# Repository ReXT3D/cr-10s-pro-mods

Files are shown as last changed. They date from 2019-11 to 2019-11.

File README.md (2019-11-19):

# Creality CR-10S Pro hardware mods
### Boards
* [Ribbon cable breakdown board](RibbonCable_MB_BreakdownBoard/) - is fully compatible with original transfer board, helps with wiring with non-original motherboards.

changes from fork
- Beefed up trace width where possible. 
- Heater PCB trace has trace on both Front and Back.
- Heater connector changed to  a more standard 5.08mm screw terminal
- and added I2C AT24C256 EEPROM 

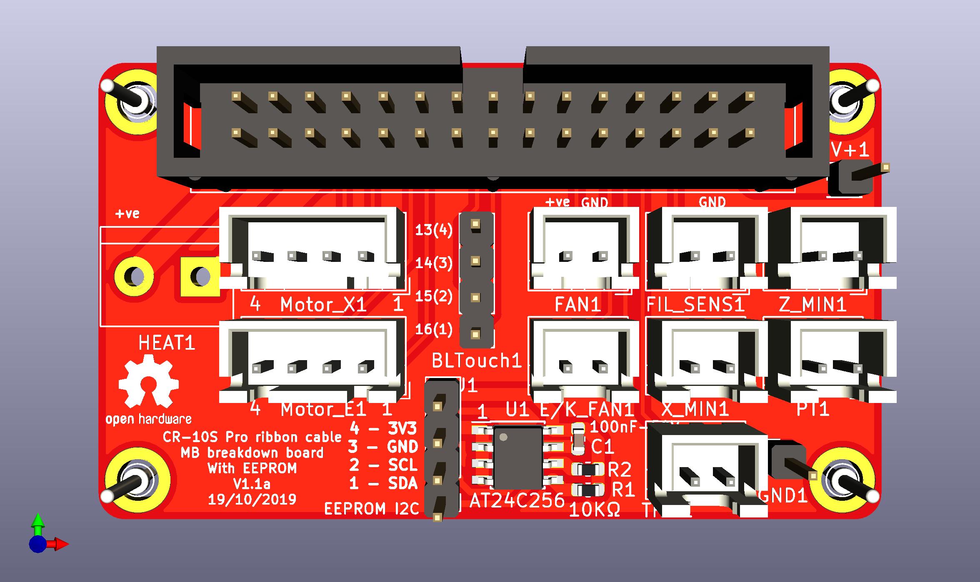
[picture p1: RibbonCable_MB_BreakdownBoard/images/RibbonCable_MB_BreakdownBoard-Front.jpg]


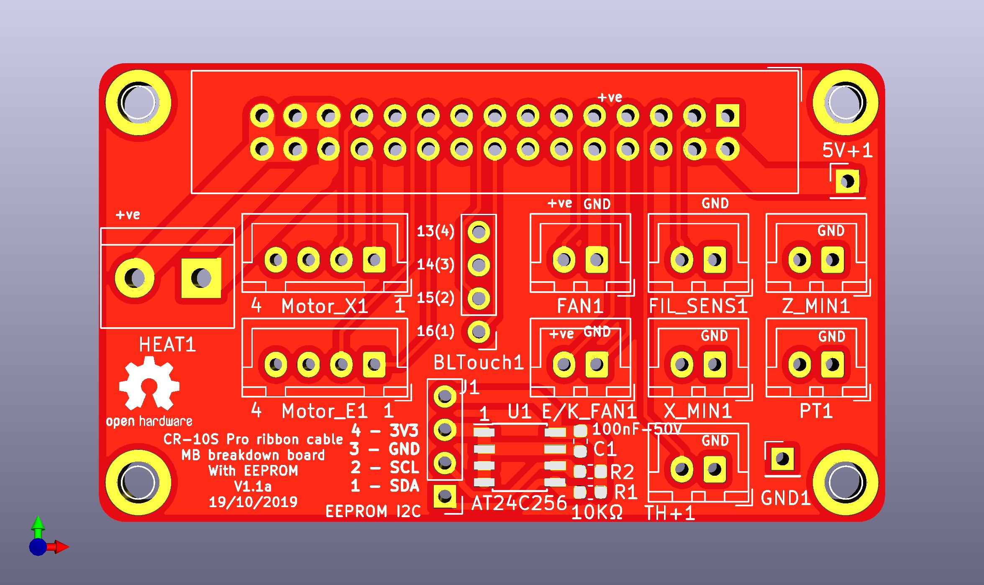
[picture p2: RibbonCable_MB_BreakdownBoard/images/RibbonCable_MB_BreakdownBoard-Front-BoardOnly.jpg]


* [Ribbon cable breakdown board (pt)](RibbonCable_MB_BreakdownBoard_pt/) - "pig tail" soldering oriented, semi compatible with original transfer board, but fully compatible with [Transfer board](Transfer_Board/). Has dedicated 4-wire connection for BLTouch and 3-wire connector for LED.


* [Transfer board](Transfer_Board/) - clean transfer board, compatible with [Ribbon cable breakdown board (pt)](RibbonCable_MB_BreakdownBoard_pt/).


#### Wiring examples
*Coming soon*

#### Ready made boards
*Photos coming soon*

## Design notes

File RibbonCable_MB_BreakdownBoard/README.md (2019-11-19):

# Ribbon cable breakdown board
It is fully compatible with [original transfer board](https://www.aliexpress.com/item/33040303019.html), helps with wiring with non-original motherboards.

FYI, it you just want the gerber files go to 
https://github.com/SkullKill/cr-10s-pro-mods/releases

changes from fork
- Beefed up trace width where possible. 
- Heater PCB trace has trace on both Front and Back.
- Heater connector changed to  a more standard 5.08mm screw terminal
- and added I2C AT24C256 EEPROM 

Front
Front-BoardOnly
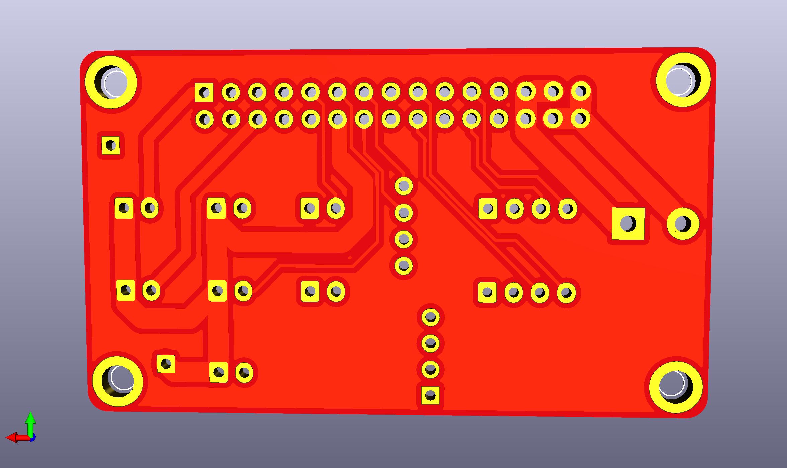
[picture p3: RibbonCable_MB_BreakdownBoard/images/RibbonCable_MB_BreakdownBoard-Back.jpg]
Back

Size

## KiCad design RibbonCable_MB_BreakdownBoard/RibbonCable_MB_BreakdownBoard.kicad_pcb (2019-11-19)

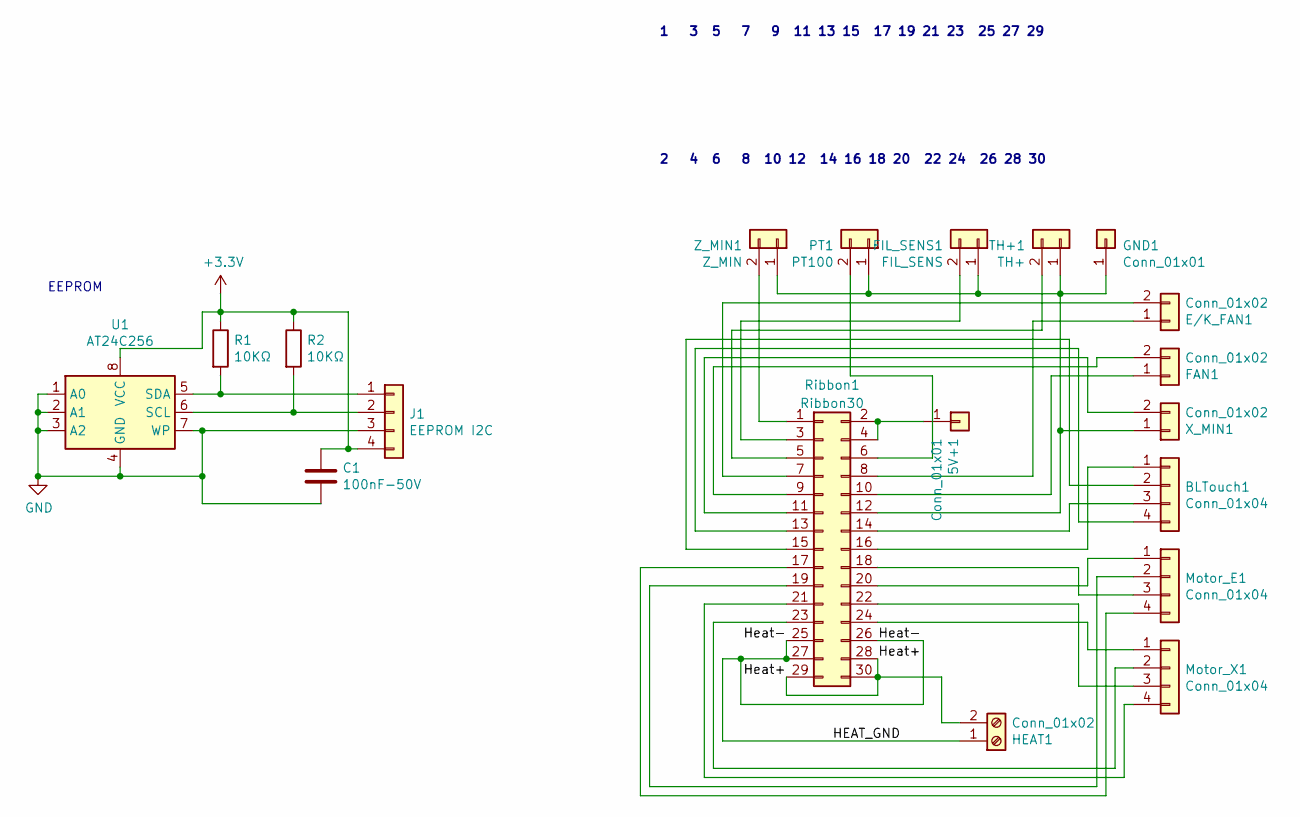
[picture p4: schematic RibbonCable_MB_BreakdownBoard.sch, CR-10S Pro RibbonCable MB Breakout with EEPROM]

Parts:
5V+1: Conn_01x01; PinHeader_1x01_P2.54mm_Vertical
BLTouch1: Conn_01x04; PinHeader_1x04_P2.54mm_Vertical
C1: 100nF-50V; C_0603_1608Metric; MPN AC0603KRX7R9BB104; LCSC C149620
E/K_FAN1: Conn_01x02; JST_XH_B2B-XH-A_1x02_P2.50mm_Vertical
FAN1: Conn_01x02; JST_XH_B2B-XH-A_1x02_P2.50mm_Vertical
FIL_SENS1: FIL_SENS; JST_XH_B2B-XH-A_1x02_P2.50mm_Vertical
GND1: Conn_01x01; PinHeader_1x01_P2.54mm_Vertical
HEAT1: Conn_01x02; TerminalBlock_bornier-2_P5.08mm; MPN KF128-2.54-4P
J1: EEPROM I2C; PinHeader_1x04_P2.54mm_Vertical
Motor_E1: Conn_01x04; JST_XH_B4B-XH-A_1x04_P2.50mm_Vertical
Motor_X1: Conn_01x04; JST_XH_B4B-XH-A_1x04_P2.50mm_Vertical
PT1: PT100; JST_XH_B2B-XH-A_1x02_P2.50mm_Vertical
R1, R2: 10KΩ; R_0603_1608Metric; MPN RC0603FR-0710KL; LCSC C98220
Ribbon1: Ribbon30; IDC-Header_2x15_P2.54mm_Vertical; MPN C79824; LCSC C79824
TH+1: TH+; JST_XH_B2B-XH-A_1x02_P2.50mm_Vertical
U1: AT24C256; SOIC-8_3.9x4.9mm_P1.27mm; MPN AT24C256C-SSHL-T; LCSC C6482
X_MIN1: Conn_01x02; JST_XH_B2B-XH-A_1x02_P2.50mm_Vertical
Z_MIN1: Z_MIN; JST_XH_B2B-XH-A_1x02_P2.50mm_Vertical

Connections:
+3V3: C1.1, J1.4, R1.1, R2.1, U1.8 (VCC)
/HEAT_GND: HEAT1.1, Ribbon1.25, Ribbon1.26, Ribbon1.27
/Heat+: HEAT1.2, Ribbon1.28, Ribbon1.29, Ribbon1.30
GND: C1.2, J1.3, U1.1 (A0), U1.2 (A1), U1.3 (A2), U1.4 (GND), U1.7 (WP)
unnamed: 5V+1.1, Ribbon1.2, Ribbon1.4
unnamed: BLTouch1.1, Ribbon1.16
unnamed: BLTouch1.2, Ribbon1.15
unnamed: BLTouch1.3, Ribbon1.14
unnamed: BLTouch1.4, Ribbon1.13
unnamed: E/K_FAN1.1, Ribbon1.8
unnamed: E/K_FAN1.2, Ribbon1.7
unnamed: FAN1.1, Ribbon1.10
unnamed: FAN1.2, Ribbon1.9
unnamed: FIL_SENS1.1, GND1.1, PT1.1, Ribbon1.12, TH+1.1, X_MIN1.1, Z_MIN1.1
unnamed: FIL_SENS1.2, Ribbon1.3
unnamed: J1.1, R1.2, U1.5 (SDA)
unnamed: J1.2, R2.2, U1.6 (SCL)
unnamed: Motor_E1.1, Ribbon1.20
unnamed: Motor_E1.2, Ribbon1.19
unnamed: Motor_E1.3, Ribbon1.18
unnamed: Motor_E1.4, Ribbon1.17
unnamed: Motor_X1.1, Ribbon1.24
unnamed: Motor_X1.2, Ribbon1.23
unnamed: Motor_X1.3, Ribbon1.22
unnamed: Motor_X1.4, Ribbon1.21
unnamed: PT1.2, Ribbon1.6
unnamed: Ribbon1.1, Z_MIN1.2
unnamed: Ribbon1.5, TH+1.2
unnamed: Ribbon1.11, X_MIN1.2

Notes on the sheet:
2 4 6 8 10 12 14 16 18 20 22 24 26 28 30
1 3 5 7 9 11 13 15 17 19 21 23 25 27 29
EEPROM

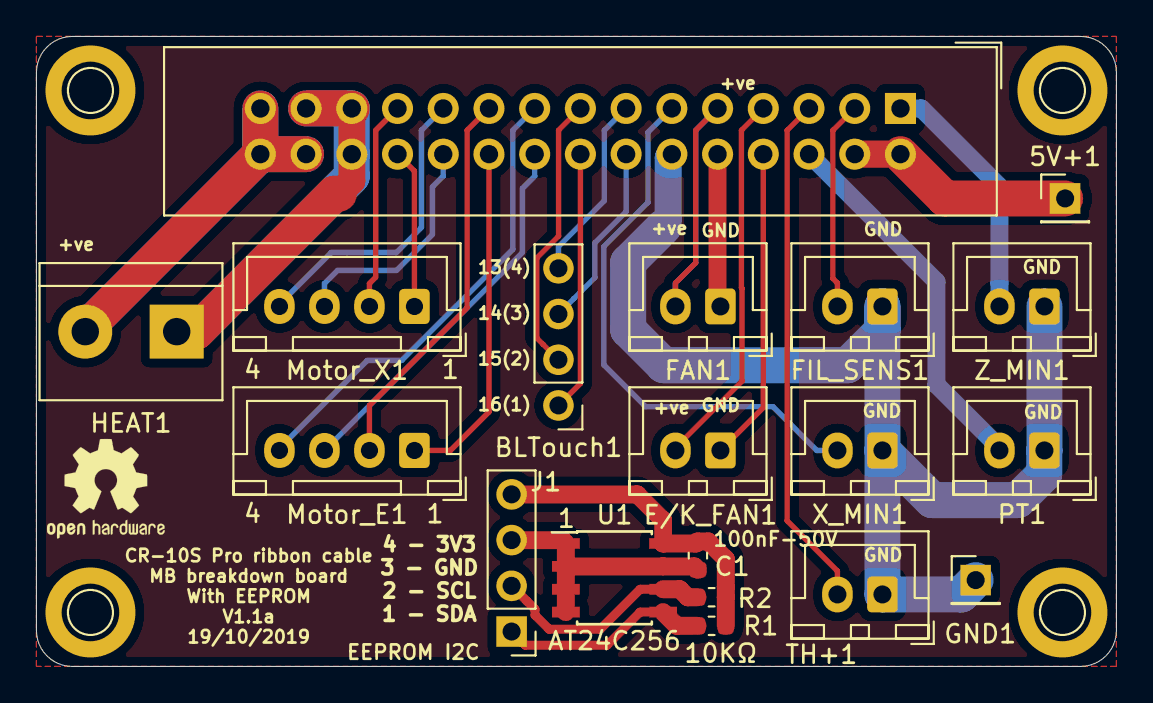
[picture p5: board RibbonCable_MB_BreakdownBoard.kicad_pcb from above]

Board: 2 copper layers, 60.0 x 35.0 mm, 19 parts (0 on the bottom side), 29 nets.

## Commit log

2019-10-14 beefed up trace and added EEPROM
    Beefed up trace width where possible.
    Heater PCB trace has trace on both Front and Back.
    Heater connector changed to a more standard 5.08mm screw terminal
    and added I2C AT24C256 EEPROM
    [RibbonCable_MB_BreakdownBoard.kicad_pcb, RibbonCable_MB_BreakdownBoard.sch]
2019-11-19 updated silkscreen to have more info
    [RibbonCable_MB_BreakdownBoard.kicad_pcb, RibbonCable_MB_BreakdownBoard.sch]
